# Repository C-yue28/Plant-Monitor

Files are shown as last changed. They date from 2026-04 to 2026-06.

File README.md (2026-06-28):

<h1>Plant Monitor</h1> 

This smart, fully automated plant monitor system monitors soil moisture, atmospheric temperature/pressure, and humidity to determine when to water the plant, and then uses a small pump to water the plant. This is meant to be a project where I learn how to design a PCB, and it is also my first project with HackClub so I am getting used to this type of work. I kept it somewhat simple this time; if my custom devboard is successful I plan to build upon this project in the future and create an automated gardening system with a web dashboard.

The PCB in this project uses an RP2040 microcontroller. The power can either be supplied through USB connection or battery; when the USB is plugged in it charges the battery and takes priority in powering the RP2040 as well. The main external modules are: BME280 for temperature/humidity/pressure sensing, SSD1315 OLED display to display some basic information to user such as soil moisture/time till next watering, Maker Soil Moisture Sensor, 1S LiPo battery for power, and 4.5V DC water pump for a cheap way to water the plant. I also found some cheap tubing for the water pump as well. Below are pictures of the main PCB and the full assembly (with the small PCB for the BME280 as well). The tank for the water will be a separate plastic container; the DC motor is submersible (IP68) and so I can just directly place it in the water. 

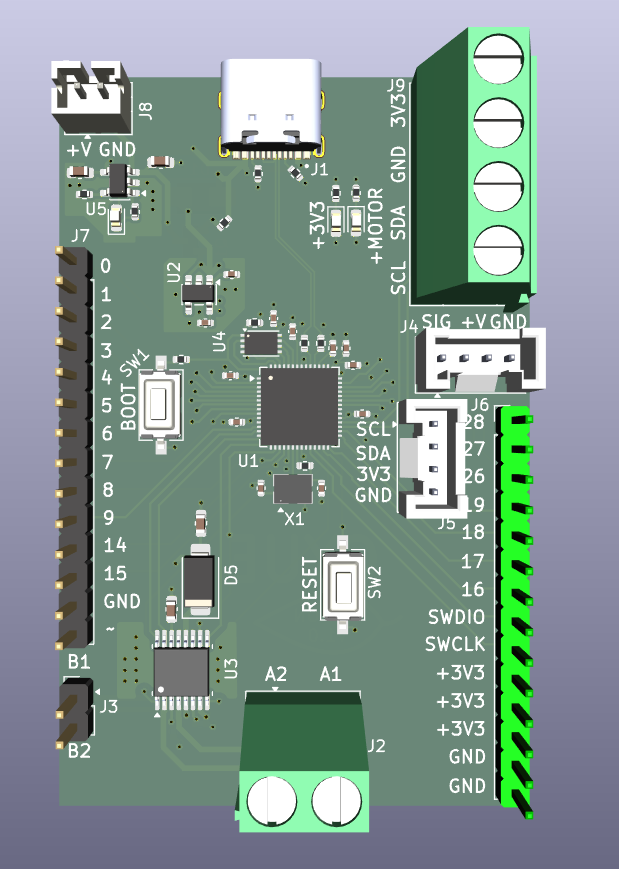
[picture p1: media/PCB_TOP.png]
PCB Top

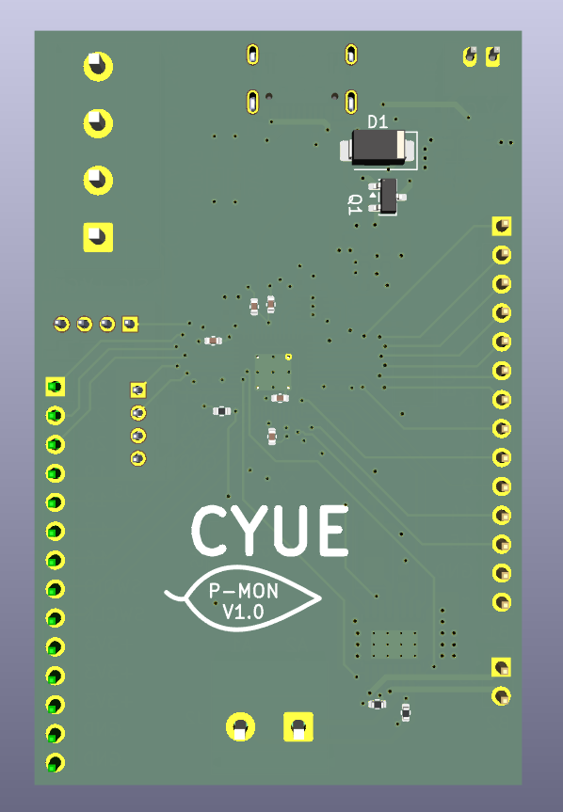
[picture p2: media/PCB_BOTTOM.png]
PCB Bottom

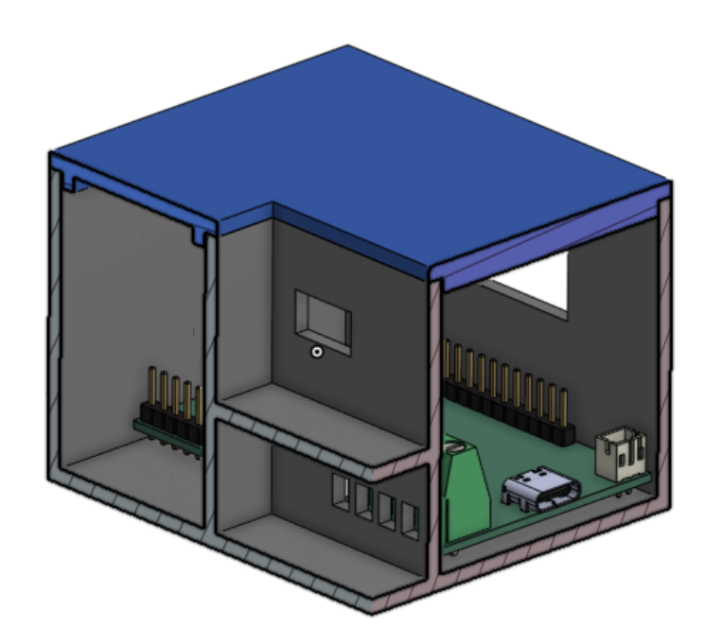
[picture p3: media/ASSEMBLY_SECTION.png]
Assembly

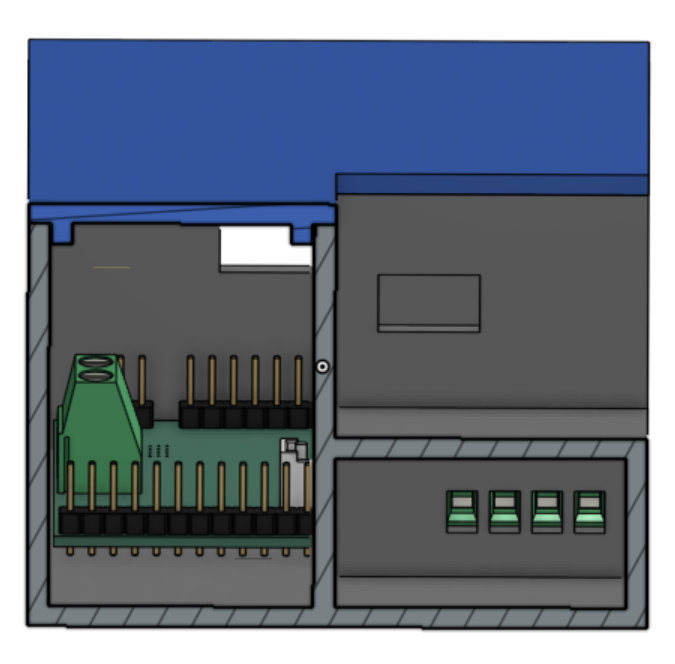
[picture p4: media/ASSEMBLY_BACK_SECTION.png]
Assembly Section View Back

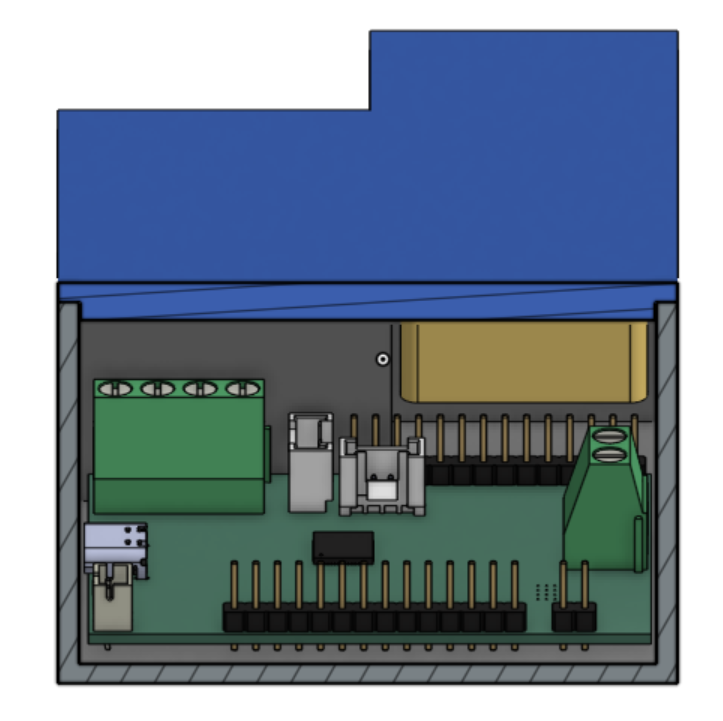
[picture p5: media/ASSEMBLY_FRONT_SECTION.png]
Assembly Section View Front

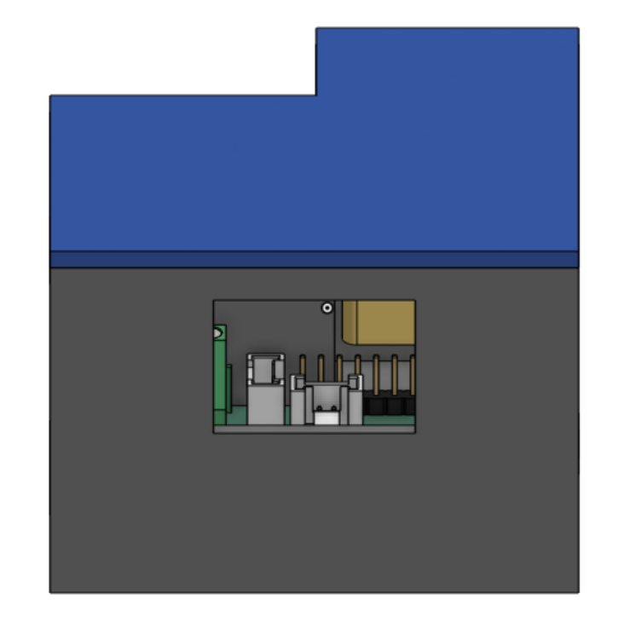
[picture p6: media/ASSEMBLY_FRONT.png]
Assembly Section View Front

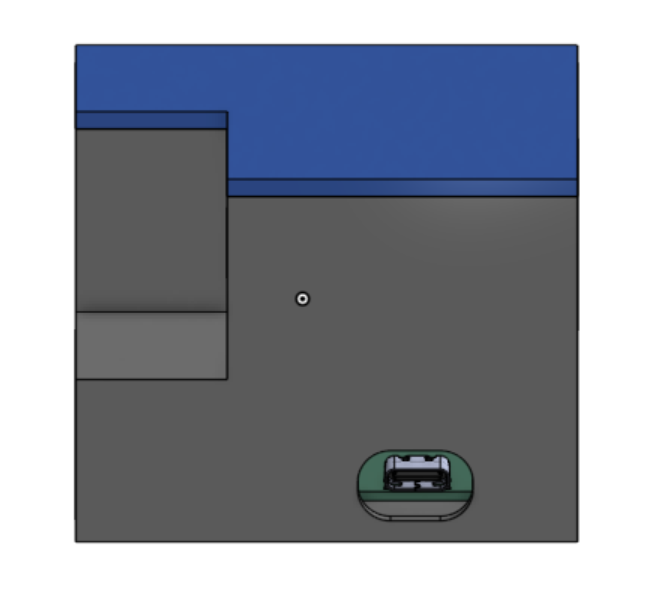
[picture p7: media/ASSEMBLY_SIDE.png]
Assembly Section View Front

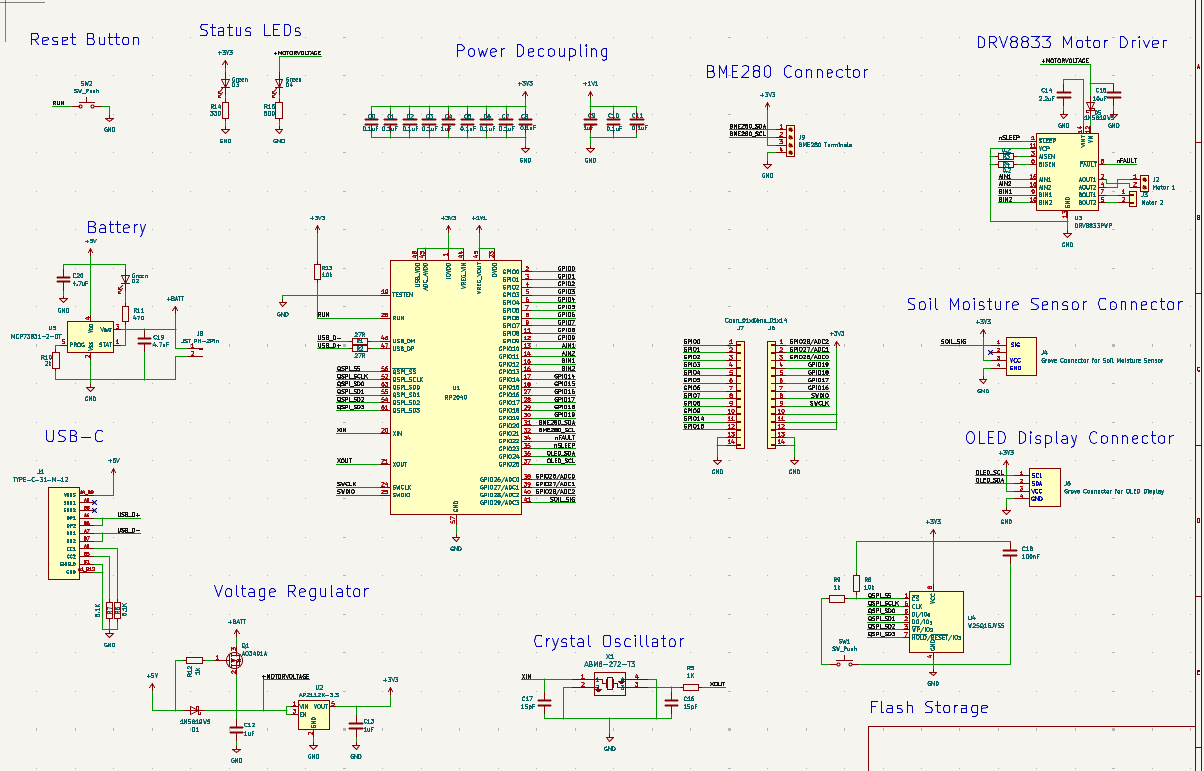
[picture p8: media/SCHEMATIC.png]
Schematic

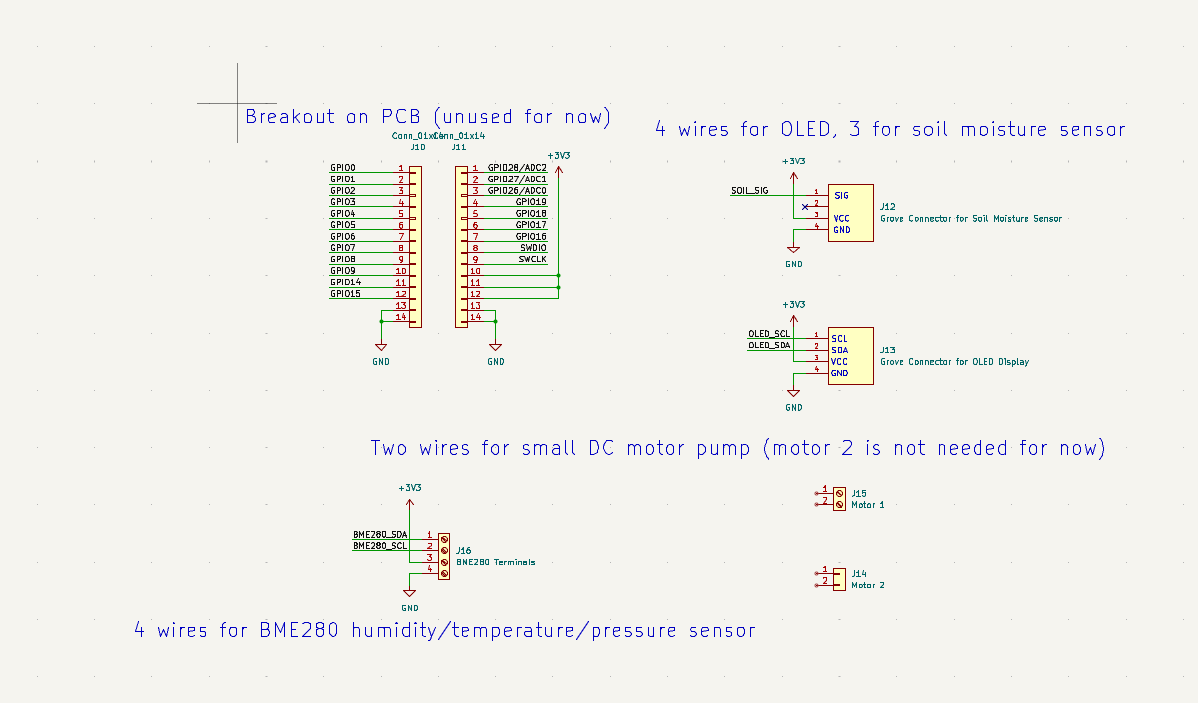
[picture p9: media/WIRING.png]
Wiring Diagram

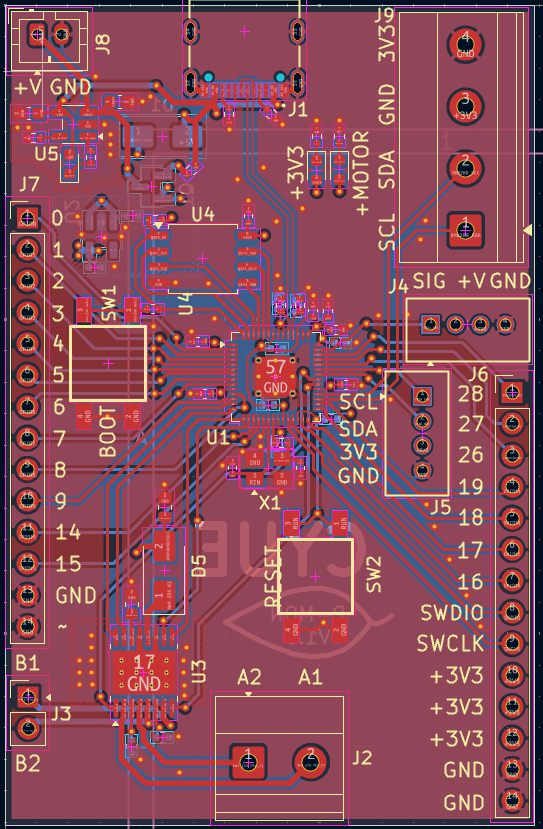
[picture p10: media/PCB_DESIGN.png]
PCB design


How is this plant monitor more intelligent than others? Well, I decided to train a machine learning model on the gathered data so that it can predict the time until the next watering, which allows the user to know when to refill the water in the tank. To do this, I added time of day and then did some data augmenting. Specifically, I added some features to the data like moisture rate changes over the past 1, 3, and 6 hours to allow the model to understand how moisture is changing over time, and I also calculated the actual time until the next watering to allow for back propagation. The model's prediction is usually within +- XXX% of the actual time, which I believe is more than sufficient. External wiring is extremely minimal; the only thing which I hooked up was a button (on a breadboard) to pin 19 which connects to ground when pressed and toggles the OLED display. The BME280 breakout is also located on that same breadboard; OLED is secured to the gap in the front of the case and connected to the Grove connector; the soil moisture sensor is connected to the Grove connector and stuck into the soil; the DC motor is connected to the screw terminals and submersed in a separate plastic water tank. The battery is housed in the back corner of the case and connected into the JST 2P terminal. 

Bill of materials (the PCB-specific BOM can be found in the production folder)

| Name | Purpose | Quantity | Total Cost (USD) | Link | Distributor  |
|---|---|---|---|---|---|
| Grove Connectors | JLCPCB is out of stock so I need to get these and solder them myself | 1 | 0.99 | http://seeedstudio.com/Grove-Universal-4-pin-connector.html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 | Seeed Studio |
| Grove Cables (5pc) | Connect the modules which have the Grove connectors | 1 | 3.2 | https://www.seeedstudio.com/Grove-Universal-4-Pin-20cm-Unbuckled-Cable-5-PCs-Pack-p-749.html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 | Seeed Studio |
| PVC tubing | Tubing for DC water pump to transport water to plant | 1 | 1.5 | https://www.adafruit.com/product/4545 | Adafruit |
| 0.96"" OLED Display  | To display information to user (soil humidity, time until next watering) | 1 | 5.5 | https://www.electromaker.io/shop/product/grove-oled-yellowblue-display-096-ssd1315-spiiic-33v5v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 | Electromaker |
| LiPo battery | To power the RP2040 so that I don't need to keep the USB plugged into something - modular design | 1 | 7.95 | https://www.digikey.com/en/products/detail/adafruit-industries-llc/1578/5054539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 | Digikey |
| Soil Moisture Sensor | To sense soil moisture. Comes with the Grove cable | 1 | 6.5 | https://www.digikey.com/en/products/detail/seeed-technology-co-ltd/101020614/10451856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 | Digikey |
| 4.5V DC Water Pump | To pump water so that the plants can be watered. | 1 | 3 | https://www.digikey.com/en/products/detail/pimoroni-ltd/COM3700/17095207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 | Digikey |
| Main PCB | Main devboard of the project | 1 | 54.81 | https://www.jlcpcb.com | JLCPCB |
| BME280 | Breakout is cheaper than PCB assembly so I decided to get a breakout of the BME280 for sensing rather than PCB | 1 | 15.99 | https://www.digikey.com/en/products/detail/sb-components-ltd/SKU27347/26694343 | Digikey |
| 3D Printed Case | To house the electronics | 1 | N/A | N/A | Self-printed |

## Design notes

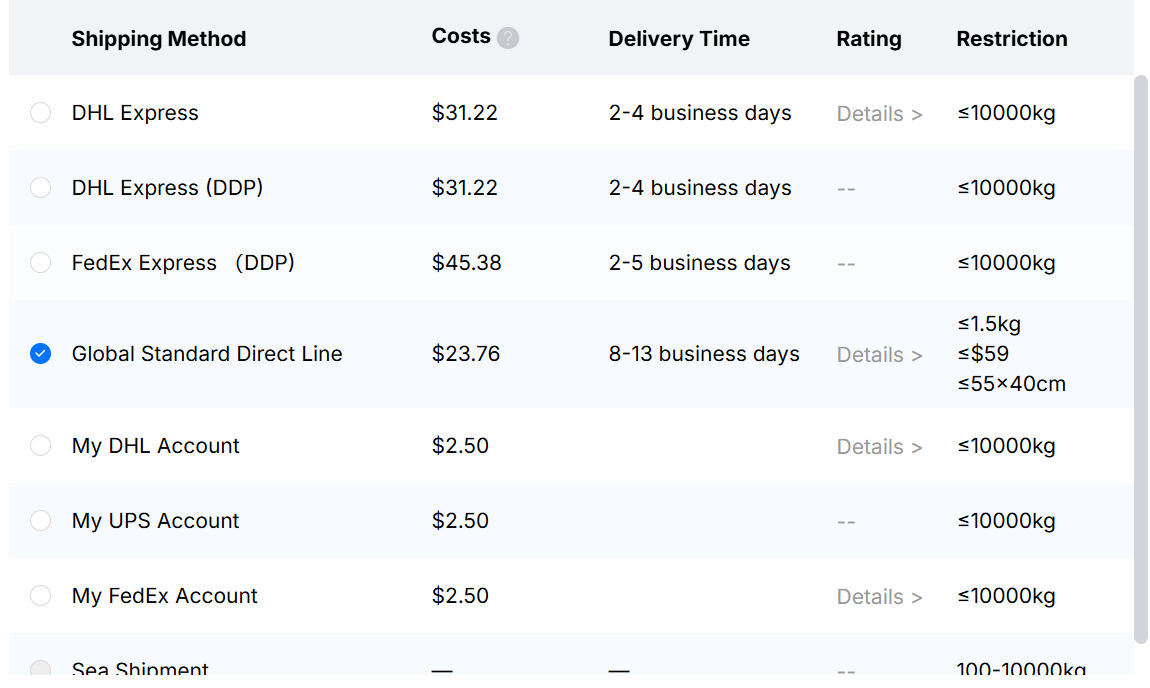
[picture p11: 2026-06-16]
media/shipping-method.png

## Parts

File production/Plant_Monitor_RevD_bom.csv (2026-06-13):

Designator | Footprint | Quantity | Value | JLCPCB Part #
C0, C1, C10, C11, C2, C3, C5, C6, C7, C8 | 0402 | 10 | 0.1uF | C1525
C12, C13, C4, C9 | 0402 | 4 | 1uF | C967571
C14 | 0603 | 1 | 2.2uF | C23630
C15 | 0603 | 1 | 10uF | C19702
C16, C17 | 0402 | 2 | 15pF | C1548
C18 | 0402 | 1 | 100nF | C1525
C19, C20 | 0603 | 2 | 4.7uF | C19666
D1, D5 | D_SMA | 2 | 1N5819WS | C82443
D2, D3, D4 | 0603 | 3 | Green | C965804
J1 | HRO_TYPE-C-31-M-12 | 1 | TYPE-C-31-M-12 | C165948
J2 | TerminalBlock_Phoenix_MKDS-1,5-2-5.08_1x02_P5.08mm_Horizontal | 1 | Motor 1 | C8269
J3 | PinHeader_1x02_P2.54mm_Vertical | 1 | Motor 2 | C32713268
J4 | SEEED_110990030 | 1 | Grove Connector for Soil Moisture Sensor
J5 | SEEED_110990030 | 1 | Grove Connector for OLED Display
J6, J7 | PinHeader_1x14_P2.54mm_Vertical | 2 | Conn_01x14 | C2894937
J8 | JST_PH_B2B-PH-K_1x02_P2.00mm_Vertical | 1 | JST PH-2Pin | C131337
J9 | TerminalBlock_Phoenix_MKDS-1,5-4_1x04_P5.00mm_Horizontal | 1 | BME280 Terminals | C192769
Q1 | SOT-23 | 1 | AO3401A | C15127
R1, R2 | 0402 | 2 | 27R | C138021
R10 | 0402 | 1 | 2k | C852711
R11 | 0402 | 1 | 470 | C851837
R12, R5, R9 | 0402 | 3 | 1k | C11702
R13, R8 | 0402 | 2 | 10k | C25744
R14 | 0402 | 1 | 330 | C25104
R15 | 0402 | 1 | 500 | C2909366
R3, R4 | 0402 | 2 | 0.2 | C7467478
R6, R7 | 0402 | 2 | 5.1K | C2906874
SW1, SW2 | SW_Tactile_SPST_NO_Straight_CK_PTS636Sx25SMTRLFS | 2 | SW_Push | C879344
U1 | QFN-56-1EP_7x7mm_P0.4mm_EP3.2x3.2mm_ThermalVias | 1 | RP2040 | C2040
U2 | SOT-23-5 | 1 | AP2112K-3.3 | C23380830
U3 | HTSSOP-16-1EP_4.4x5mm_P0.65mm_EP3.4x5mm_Mask2.46x2.31mm_ThermalVias | 1 | DRV8833PWP | C191171
U4 | SOIC-8_5.3x5.3mm_P1.27mm | 1 | W25Q16JVSS | C82317
U5 | SOT-23-5 | 1 | MCP73831-2-OT | C14879
X1 | ABM8-272-T3_ABR | 1 | ABM8-272-T3 | C20625731

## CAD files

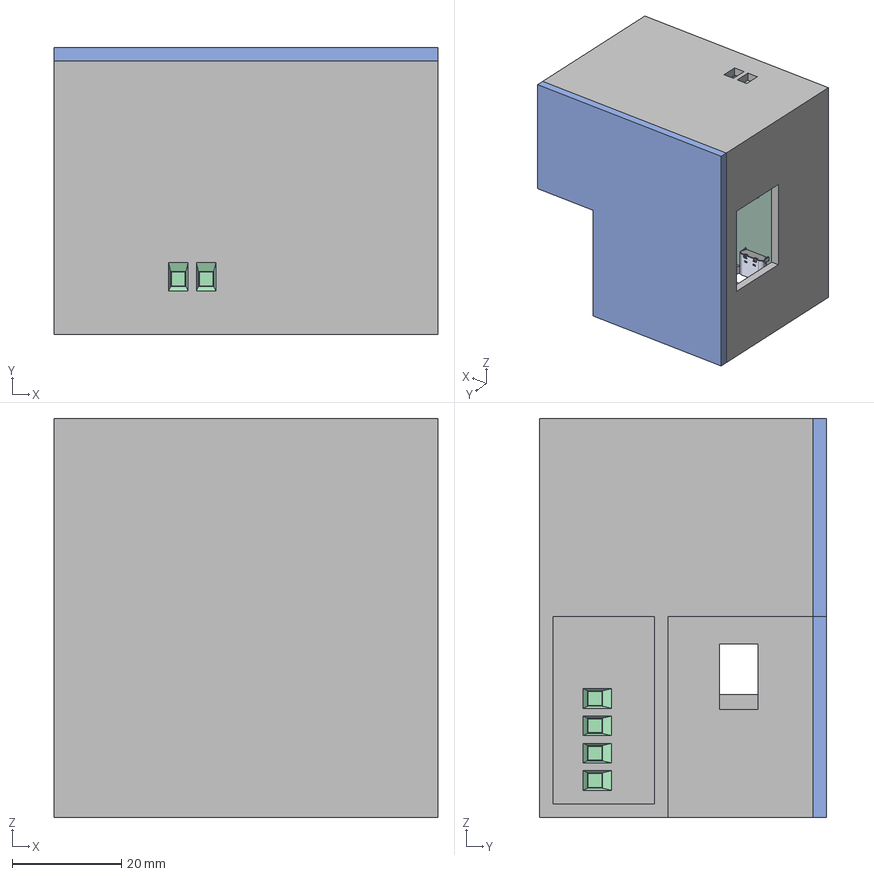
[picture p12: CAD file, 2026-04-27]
CAD/Main Assembly.step
70.2 x 52.5 x 73.0 mm
TerminalBlock_Phoenix_MKDS-1,5-2-5.08_1x02_P5.08mm_Horizontal
110990030--3DModel-STEP-56544 x 5
500mAh battery v1
TerminalBlock_Phoenix_MKDS-1,5-4_1x04_P5.00mm_Horizontal
QFN-56-1EP_7x7mm_P0.4mm_EP3.2x3.2mm
PinHeader_1x14_P2.54mm_Vertical
Main PCB Enclosure
Lid
110990030--3DModel-STEP-56544_1 x 5
JST_PH_B2B-PH-K_1x02_P2.00mm_Vertical
PinHeader_1x02_P2.54mm_Vertical
PinHeader_1x14_P2.54mm_Vertical_1
Plant Monitor_PCB
TYPE-C-31-M-12 x 2

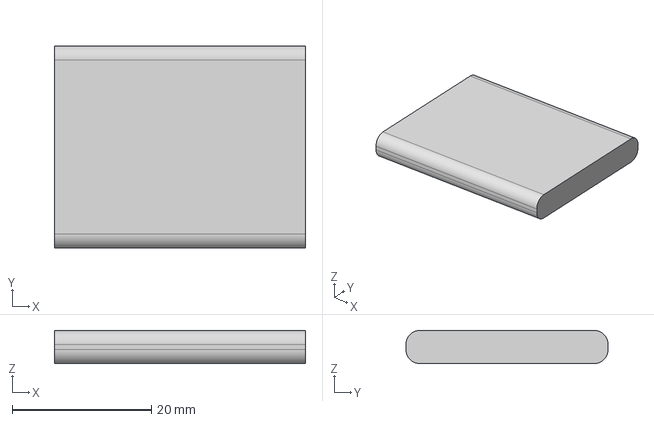
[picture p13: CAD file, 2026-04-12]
CAD/Parts/1578 500mAh battery.step
36.0 x 29.0 x 4.75 mm

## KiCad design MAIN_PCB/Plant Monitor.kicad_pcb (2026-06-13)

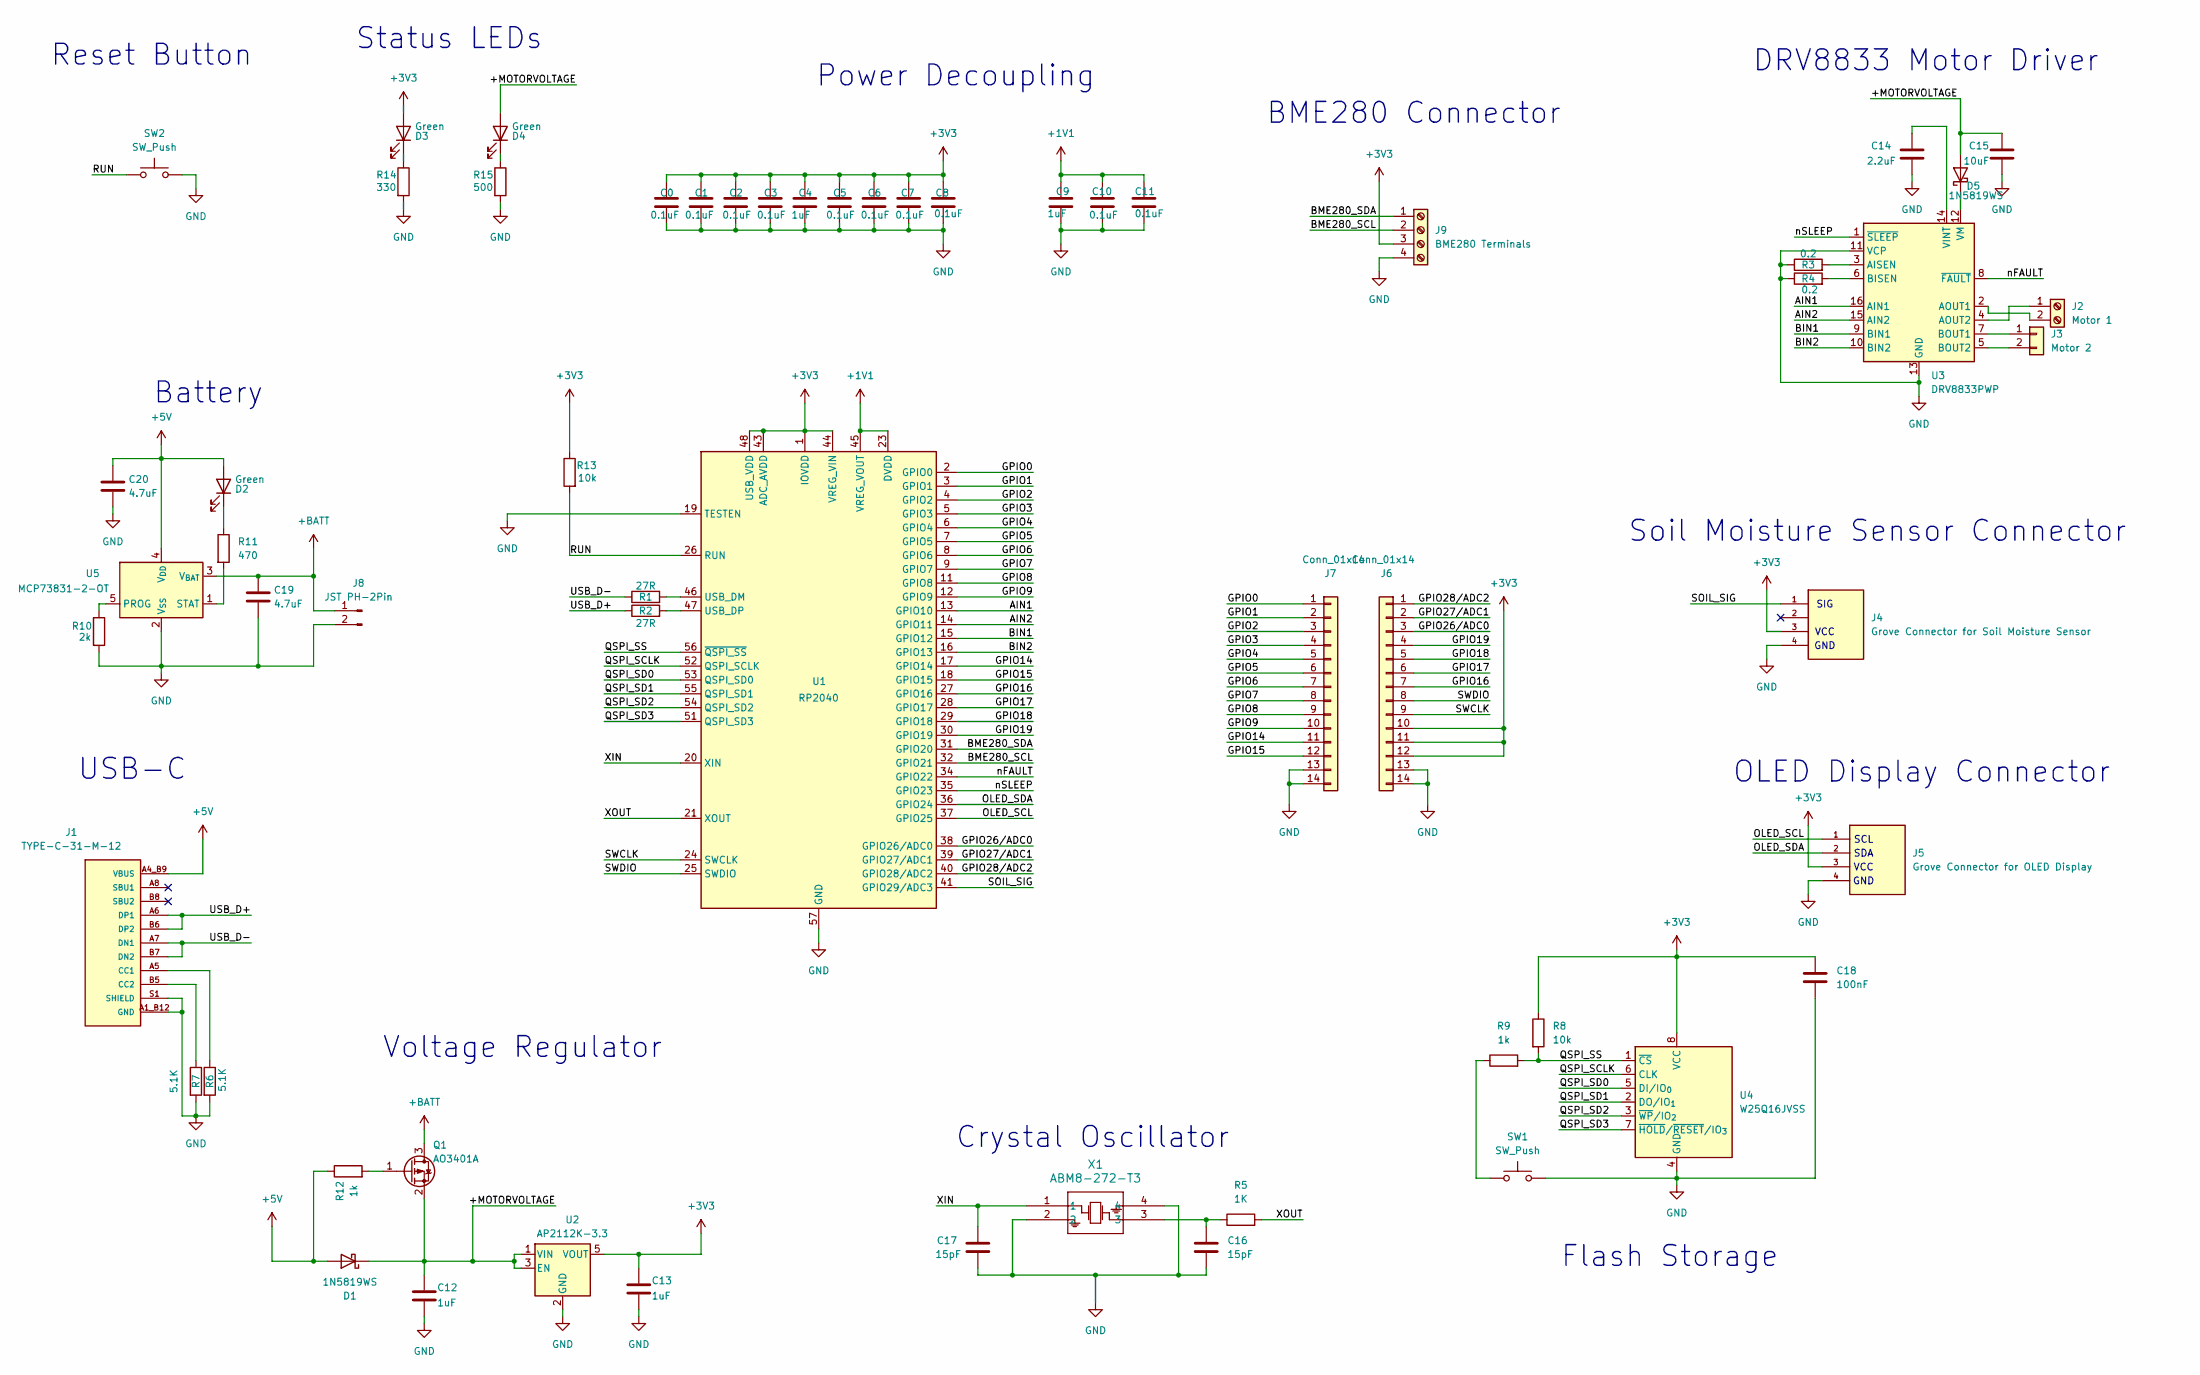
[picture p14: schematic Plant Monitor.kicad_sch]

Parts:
C0, C1, C2, C3, C5, C6, C7, C8, C10, C11: 0.1uF; C_0402_1005Metric
C4, C9, C12, C13: 1uF; C_0402_1005Metric
C14: 2.2uF; C_0603_1608Metric
C15: 10uF; C_0603_1608Metric
C16, C17: 15pF; C_0402_1005Metric
C18: 100nF; C_0402_1005Metric
C19, C20: 4.7uF; C_0603_1608Metric
D1, D5: 1N5819WS; D_SMA
D2, D3, D4: Green; LED_0603_1608Metric
J1: TYPE-C-31-M-12; HRO_TYPE-C-31-M-12; PARTREV 2020.12.08
J2: Motor 1; TerminalBlock_Phoenix_MKDS-1,5-2-5.08_1x02_P5.08mm_Horizont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
J3: Motor 2; PinHeader_1x02_P2.54mm_Vertical
J4: Grove Connector for Soil Moisture Sensor; SEEED_110990030; PARTREV A
J5: Grove Connector for OLED Display; SEEED_110990030; PARTREV A
J6, J7: Conn_01x14; PinHeader_1x14_P2.54mm_Vertical
J8: JST PH-2Pin; JST_PH_B2B-PH-K_1x02_P2.00mm_Vertical
J9: BME280 Terminals; TerminalBlock_Phoenix_MKDS-1,5-4_1x04_P5.00mm_Horizontal
Q1: AO3401A; SOT-23
R1, R2: 27R; R_0402_1005Metric
R3, R4: 0.2; R_0402_1005Metric
R5: 1K; R_0402_1005Metric
R6, R7: 5.1K; R_0402_1005Metric
R8, R13: 10k; R_0402_1005Metric
R9, R12: 1k; R_0402_1005Metric
R10: 2k; R_0402_1005Metric
R11: 470; R_0402_1005Metric
R14: 330; R_0402_1005Metric
R15: 500; R_0402_1005Metric
SW1, SW2: SW_Push; SW_Tactile_SPST_NO_Straight_CK_PTS636Sx25SMTRLFS
U1: RP2040; QFN-56-1EP_7x7mm_P0.4mm_EP3.2x3.2mm_ThermalVias
U2: AP2112K-3.3; SOT-23-5
U3: DRV8833PWP; HTSSOP-16-1EP_4.4x5mm_P0.65mm_EP3.4x5mm_Mask2.46x2.31mm_The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
U4: W25Q16JVSS; SOIC-8_5.3x5.3mm_P1.27mm
U5: MCP73831-2-OT; SOT-23-5
X1: ABM8-272-T3; ABM8-272-T3_ABR

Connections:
+1V1: C9.1, C10.1, C11.1, U1.23 (DVDD), U1.45 (VREG_VOUT), U1.50 (DVDD)
+3V3: C0.1, C1.1, C2.1, C3.1, C4.1, C5.1, C6.1, C7.1, C8.1, C13.1, C18.1, D3.2 (A), J4.3, J5.3, J6.10, J6.11, J6.12, J9.3, R8.1, R13.1, U1.1 (IOVDD), U1.10 (IOVDD), U1.22 (IOVDD), U1.33 (IOVDD), U1.42 (IOVDD), U1.43 (ADC_AVDD), U1.44 (VREG_VIN), U1.48 (USB_VDD), U1.49 (IOVDD), U2.5 (VOUT), U4.8 (VCC)
+5V: C20.1, D1.2 (A), D2.2 (A), J1.A4_B9 (VBUS), J1.B4_A9 (VBUS), R12.1, U5.4 (V_{DD})
+BATT: C19.1, J8.1, Q1.3 (D), U5.3 (V_{BAT})
/+MOTORVOLTAGE: C12.1, C15.1, D1.1 (K), D4.2 (A), D5.2 (A), Q1.2 (S), U2.1 (VIN), U2.3 (EN)
/AIN1: U1.13 (GPIO10), U3.16 (AIN1)
/AIN2: U1.14 (GPIO11), U3.15 (AIN2)
/BIN1: U1.15 (GPIO12), U3.9 (BIN1)
/BIN2: U1.16 (GPIO13), U3.10 (BIN2)
/BME280_SCL: J9.2, U1.32 (GPIO21)
/BME280_SDA: J9.1, U1.31 (GPIO20)
/GPIO0: J7.1, U1.2 (GPIO0)
/GPIO1: J7.2, U1.3 (GPIO1)
/GPIO2: J7.3, U1.4 (GPIO2)
/GPIO3: J7.4, U1.5 (GPIO3)
/GPIO4: J7.5, U1.6 (GPIO4)
/GPIO5: J7.6, U1.7 (GPIO5)
/GPIO6: J7.7, U1.8 (GPIO6)
/GPIO7: J7.8, U1.9 (GPIO7)
/GPIO8: J7.9, U1.11 (GPIO8)
/GPIO9: J7.10, U1.12 (GPIO9)
/GPIO14: J7.11, U1.17 (GPIO14)
/GPIO15: J7.12, U1.18 (GPIO15)
/GPIO16: J6.7, U1.27 (GPIO16)
/GPIO17: J6.6, U1.28 (GPIO17)
/GPIO18: J6.5, U1.29 (GPIO18)
/GPIO19: J6.4, U1.30 (GPIO19)
/GPIO26/ADC0: J6.3, U1.38 (GPIO26/ADC0)
/GPIO27/ADC1: J6.2, U1.39 (GPIO27/ADC1)
/GPIO28/ADC2: J6.1, U1.40 (GPIO28/ADC2)
/OLED_SCL: J5.1, U1.37 (GPIO25)
/OLED_SDA: J5.2, U1.36 (GPIO24)
/QSPI_SCLK: U1.52 (QSPI_SCLK), U4.6 (CLK)
/QSPI_SD0: U1.53 (QSPI_SD0), U4.5 (DI/IO_{0})
/QSPI_SD1: U1.55 (QSPI_SD1), U4.2 (DO/IO_{1})
/QSPI_SD2: U1.54 (QSPI_SD2), U4.3 (~WP/IO_{2})
/QSPI_SD3: U1.51 (QSPI_SD3), U4.7 (~HOLD/~RESET/IO_{3})
/QSPI_SS: R8.2, R9.2, U1.56 (~QSPI_SS), U4.1 (~CS)
/RUN: R13.2, SW2.1, SW2.3, U1.26 (RUN)
/SOIL_SIG: J4.1, U1.41 (GPIO29/ADC3)
/SWCLK: J6.9, U1.24 (SWCLK)
/SWDIO: J6.8, U1.25 (SWDIO)
/USB_D+: J1.A6 (DP1), J1.B6 (DP2), R2.1
/USB_D-: J1.A7 (DN1), J1.B7 (DN2), R1.1
/XIN: C17.1, U1.20 (XIN), X1.1
/XOUT: R5.2, U1.21 (XOUT)
/nFAULT: U1.34 (GPIO22), U3.8 (~FAULT)
/nSLEEP: U1.35 (GPIO23), U3.1 (~SLEEP)
GND: C0.2, C1.2, C2.2, C3.2, C4.2, C5.2, C6.2, C7.2, C8.2, C9.2, C10.2, C11.2, C12.2, C13.2, C14.2, C15.2, C16.2, C17.2, C18.2, C19.2, C20.2, J1.A1_B12 (GND), J1.B1_A12 (GND), J1.S1 (SHIELD), J1.S2 (SHIELD), J1.S3 (SHIELD), J1.S4 (SHIELD), J4.4, J5.4, J6.13, J6.14, J7.13, J7.14, J8.2, J9.4, R3.1, R4.1, R6.2, R7.2, R10.2, R14.2, R15.2, SW1.2, SW1.4, SW2.2, SW2.4, U1.19 (TESTEN), U1.57 (GND), U2.2 (GND), U3.11 (VCP), U3.13 (GND), U3.17 (GND), U4.4 (GND), U5.2 (V_{SS}), X1.2, X1.4
unnamed: C16.1, R5.1, X1.3
unnamed: D2.1 (K), R11.1
unnamed: D3.1 (K), R14.1
unnamed: D4.1 (K), R15.1
unnamed: D5.1 (K), U3.12 (VM)
unnamed: J1.A5 (CC1), R6.1
unnamed: J1.B5 (CC2), R7.1
unnamed: J2.1, U3.4 (AOUT2)
unnamed: J2.2, U3.2 (AOUT1)
unnamed: J3.1, U3.7 (BOUT1)
unnamed: J3.2, U3.5 (BOUT2)
unnamed: Q1.1 (G), R12.2
unnamed: R9.1, SW1.1, SW1.3
unnamed: R1.2, U1.46 (USB_DM)
unnamed: R2.2, U1.47 (USB_DP)
unnamed: R3.2, U3.3 (AISEN)
unnamed: R4.2, U3.6 (BISEN)
unnamed: C14.1, U3.14 (VINT)
unnamed: R10.1, U5.5 (PROG)
unnamed: R11.2, U5.1 (STAT)

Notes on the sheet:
SDA
GND
Reset Button
DRV8833 Motor Driver
Power Decoupling
VCC
USB-C
Voltage Regulator
SIG
SCL
Battery
Flash Storage
Crystal Oscillator
Status LEDs
OLED Display Connector
Soil Moisture Sensor Connector
BME280 Connector

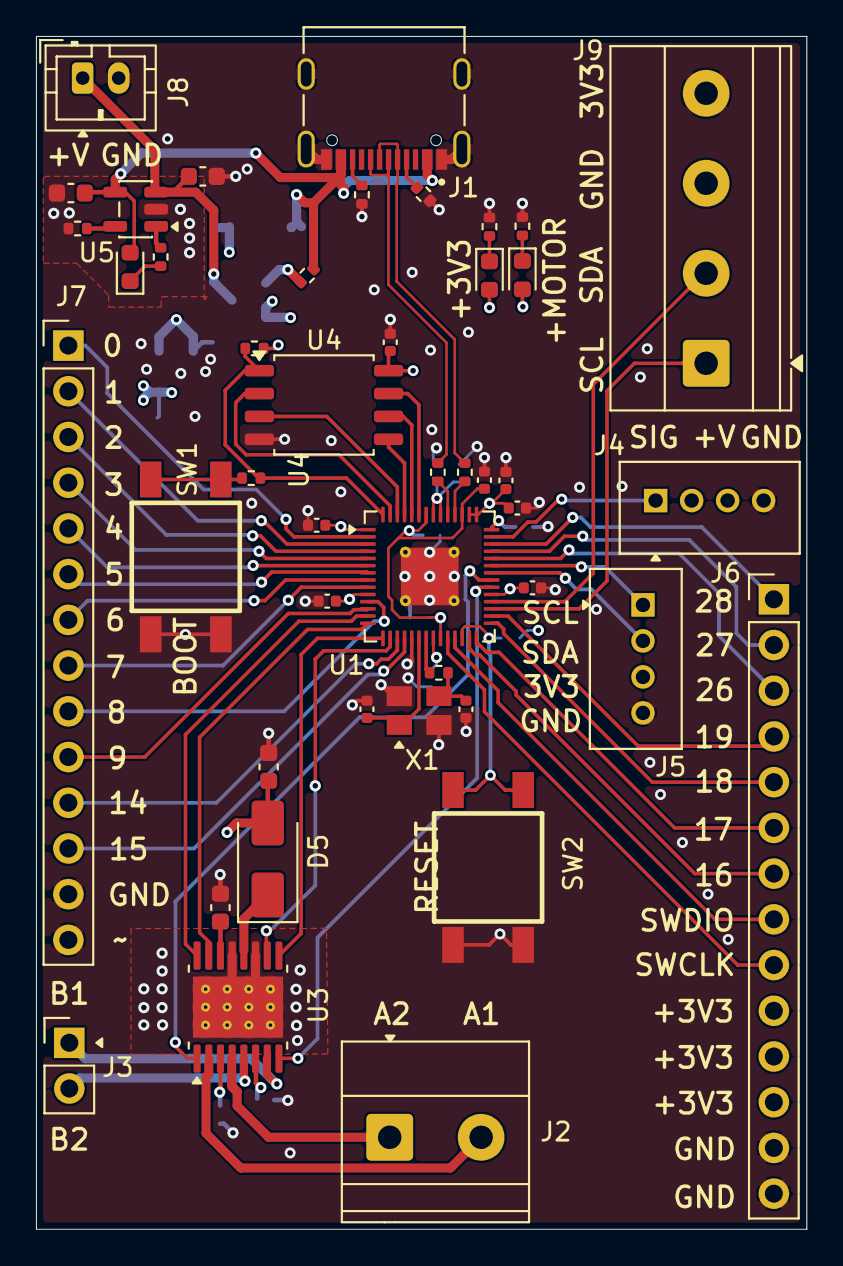
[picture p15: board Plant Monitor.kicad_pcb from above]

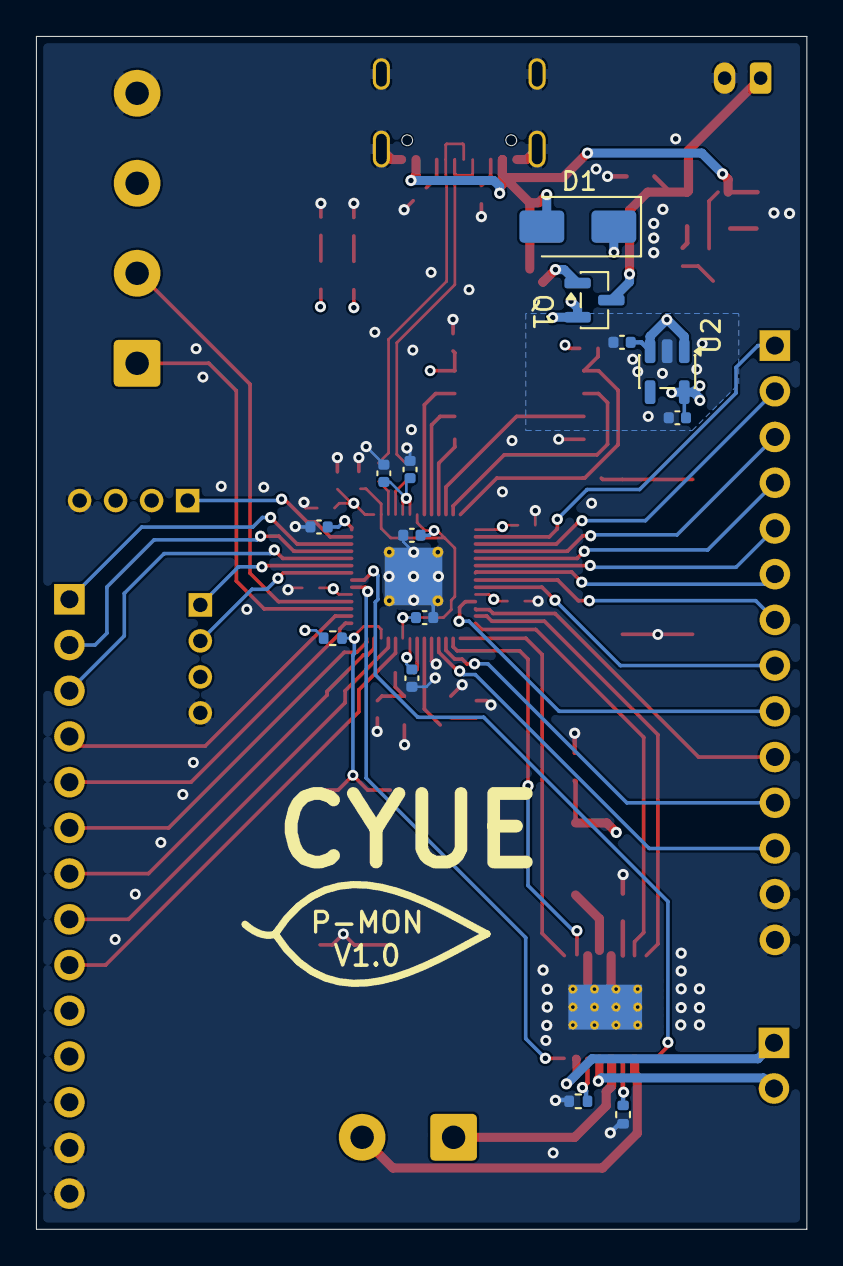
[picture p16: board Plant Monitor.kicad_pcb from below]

Board: 6 copper layers, 42.8 x 66.3 mm, 59 parts (14 on the bottom side), 69 nets.

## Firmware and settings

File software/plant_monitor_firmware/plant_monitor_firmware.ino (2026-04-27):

/*

Firmware for Plant Monitor HackClub Stasis Project

*/

#include <Wire.h>
#include <Adafruit_Sensor.h>
#include <Adafruit_BME280.h>
#include <U8x8lib.h>

// mode: normal (0) or data collection (1) (sample more often to gather data for ML model)

const int MODE = 0;
const double K;
const double a;
const double b;
const double c;

//GPIO pins:

const int AIN1 = 10;
const int AIN2 = 11;
const int SLEEP = 23;

const int BME280_SDA = 20;
const int BME280_SCL = 21;

const int OLED_SDA = 24;
const int OLED_SCL = 25;

const int SOIL_SIG = 29;

const int BUTTON = 19;

// data readings

double soil_moisture = 0;
double SOIL_MOISTURE_THRESHOLD = 0.40; // arbitrary value found online (40%)
const double M_param = pow(SOIL_MOISTURE_THRESHOLD, 1-a);

Adafruit_BME280 bme280;
double temperature;
double humidity;
double pressure;

U8X8_SSD1315_128X64_NONAME_HW_I2C oled(U8X8_PIN_NONE, OLED_SCL, OLED_SDA);
bool OLED_ON = 0;
int OLED_ON_MILLIS = 0;

// time
int timeStep = 1800000; // ms; 30 minutes

struct days_hours {
  int days;
  int hours;
}

void readData() {

  // sample each sensor multiple times; take an average
  sum_moisture = 0;
  sum_temp = 0;
  sum_hum = 0;
  sum_pressure = 0;

  for (int i = 0; i < SAMPLE_COUNT; i++) {

    // for now, I cannot know what values this will get - it is a relative measurement; as moisture goes up analog voltage goes down 
    sum_moisture += analogRead(SOIL_SIG) / 3.3; // for now I will simply take it as a percentage of its max; I will definitely have to adjust this

    sum_temp += bme280.readTemperature();
    sum_hum += bme280.readHumidity();
    sum_pressure += bme280.readPressure() / 1000.0F;

  }

  soil_moisture = sum_moisture / SAMPLE_COUNT;
  temperature = sum_temp / SAMPLE_COUNT;
  humidity = sum_hum / SAMPLE_COUNT;
  pressure = sum_pressure / SAMPLE_COUNT;

}

days_hours predictTime() {
  // integrated the rate calculation function using the assumption that (1+b*T)(1-c*H) would remain relatively constant enough for me to treat it as such
  // this was done with the help of many online sources and ChatGPT
  time_until_next_water = (M_param-pow(soil_moisture, 1-a)) / (k*(1+b*temperature)*(1-c*humidity)*(1-a))
}

void toggleDisplay() {

  if (OLED_ON) {
    OLED_ON = false;
    oled.clearDisplay();
    return;
  }

  time_until_next_water = predictTime();

  oled.drawString(0, 0, "Moisture: %.2f", soil_moisture);
  oled.drawString(0, 1, "Temp(C): %.2f", temperature);
  oled.drawString(0, 2, "Humidity: %.2f%%", humidity);
  oled.drawString(0, 3, "Pressure: %.1f atm", pressure/760.0F);
  if (!MODE) {
    oled.drawString(0, 4, "Time until next")
    oled.drawString(0, 5, "water: %d:%d", time_until_next_water.days, time_until_next_water.hours);
  }

  OLED_ON = true;
  delay(50); // debounce button

}

void outputData(bool hasWatered) {
  Serial.println("SOIL: %f", soil_moisture);
  Serial.println("TEMPERATURE: %f", temperature);
  Serial.println("HUMIDITY: %f", humidity);
  Serial.println("WATERED: %d", hasWatered ? 1 : 0);
  Serial.println("MILLIS: %f", millis()); // for calculating evaporation rate
}

void waterPlant() {
  analogWrite(AIN1, MOTOR_SPEED);
  delay(5000);
  analogWrite(AIN1, 0);
}

void setup() {

  // initialize I2C buses
  Wire.setSDA(BME280_SDA);
  Wire.setSCL(BME280_SCL);

  // Wire1.setSDA(OLED_SDA);
  // Wire1.setSCL(OLED_SCL);
  
  oled.begin();
  bme280.begin(0x76, &Wire);
  Serial.begin(115200);

  // pin modes
  pinMode(AIN1, OUTPUT);
  pinMode(AIN2, OUTPUT);
  pinMode(SLEEP, OUTPUT);
  pinMode(SOIL_SIG, INPUT);
  pinMode(BUTTON, INPUT_PULLUP);

  attachInterrupt(digitalPinToInterrupt(BUTTON), toggleDisplay, LOW);
  digitalWrite(SLEEP, HIGH);

  oled.setFont(u8x8_font_8x13_1x2_f);
  if (MODE) {
    timeStep /= 6; // 30 minutes down to 5 minutes
  }

  Serial.println("Ready.");  

}

void loop() {

  readData();

  if (soil_moisture < SOIL_MOISTURE_THRESHOLD) {
    waterPlant();
    outputData(true);
  } else {
    outputData(false);
  }

  delay(timeStep);

}

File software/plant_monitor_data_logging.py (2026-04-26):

import serial
import keyboard
import sys
import csv

from plant_monitor_data_augmentation import Data

def log_data_and_end():
    global entries
    has_been_created = True
    try:
        test_file = open("plant_monitor_data.csv", "r+")
        test_file.close()
    except:
        has_been_created = False

    with open("plant_monitor_data.csv", "a+") as data_table:
        writer = csv.writer(data_table)
        writer.writerows(entries)

    sys.exit()

SERIAL = serial.Serial(port='COM3', baudrate=115200)
keyboard.add_hotkey('q', log_data_and_end)

entries = []

while True:
    new_entry = Data()
    for i in range(5):
        serial_data = SERIAL.readline().decode("utf-8").strip()
        new_entry[i] = float(serial_data[(serial_data.find(":")+2):])
    new_entry.time /= 3600000
    entries.append(new_entry.to_raw_data())

SERIAL.close()

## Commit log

2026-03-31 Commit all project files as of right now
    [Plant Monitor.kicad_sch]
2026-03-31 First actual commit with git
    [Plant Monitor.kicad_sch]
2026-04-02 Re-commit .gitignore with new schematic included
    [Plant Monitor.kicad_sch]
2026-04-02 Finished main PCB schematic, as well as BMP280 schematic
    [BME280_PCB.kicad_pcb, BME280_PCB.kicad_sch, Plant Monitor.kicad_pcb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]
2026-04-05 Updated PCB design+schematic
    [Plant Monitor.kicad_pcb, Plant Monitor.kicad_sch]
2026-04-11 Finished main PCB
    [Plant Monitor.kicad_pcb, Plant Monitor.kicad_sch]
2026-04-12 Finished all PCBs, initial CAD complete
    [1578 500mAh battery.step, BME280_PCB.kicad_pcb, BME280_PCB.kicad_sch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]
2026-04-22 Added new item to gitignore
    [1578 500mAh battery.step, BME280_PCB.kicad_pcb, BME280_PCB.kicad_sch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]
2026-04-22 Added CAD, production files for main PCB
    [1578 500mAh battery.step, BME280_PCB.kicad_pcb, BME280_PCB.kicad_sch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]
2026-04-24 Wrote firmware for the RP2040 and began working on the implementation of the ML model
    [1578 500mAh battery.step, BME280_PCB.step, CAD Assembly.step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]
2026-04-27 Finished README, added full BOM, deleted the unnecessary BME280 PCB files
    [BME280_PCB.kicad_pcb, BME280_PCB.kicad_sch, BME280_PCB.step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]
2026-06-13 Revision D of PCB design
    [Plant Monitor.kicad_pcb, Plant Monitor.kicad_sch, Plant_Monitor_RevC_positions.csv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]
2026-06-13 Updated BOM and production details
    [Plant Monitor BOM.csv]
2026-06-17 Added wiring/schematic
    [Plant Monitor.kicad_sch]
2026-06-28 Add pcb design image
